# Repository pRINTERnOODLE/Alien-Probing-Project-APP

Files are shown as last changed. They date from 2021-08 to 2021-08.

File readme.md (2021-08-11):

### APP Alien Probing Project

Design prompts for this mod are: 
- To provide a bed probing solution for the Tiny-M which requires no modifications to the core parts and no loss of X Y or Z axis travel.

Additional design parameters include: 
- Keep the design envelope unchanged (fit inside panels etc)
- NOT affect overall design beyond adding probe functionality.
- Printed parts must not require supports

The M3x5mm hex screws used on the "captive" MUST be alloy steel and must be either flat head or cap head in order to be magnetically attracted when attaching.

Typically no brim is required for the printed parts...EXCEPT FOR THE SHUTTLE (see print settings below)

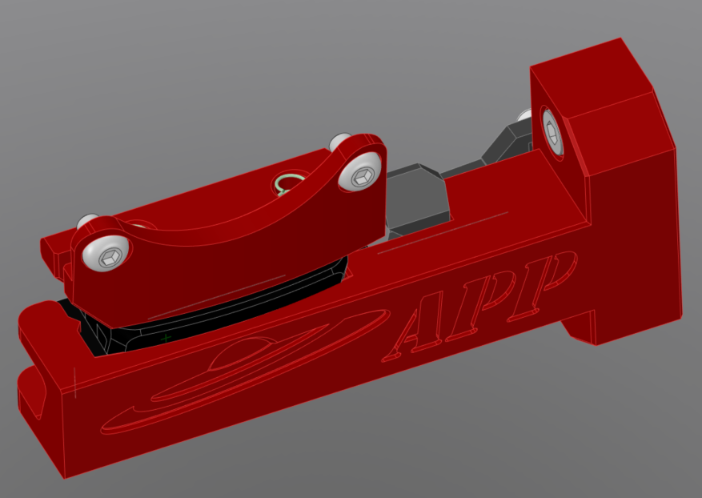
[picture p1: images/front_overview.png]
Front Overview


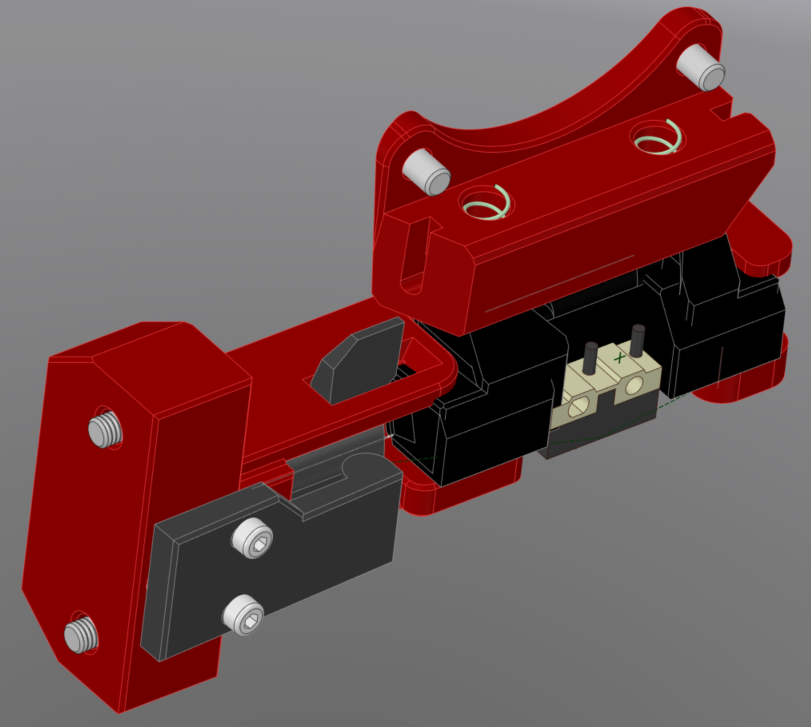
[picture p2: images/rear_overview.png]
Rear Overview


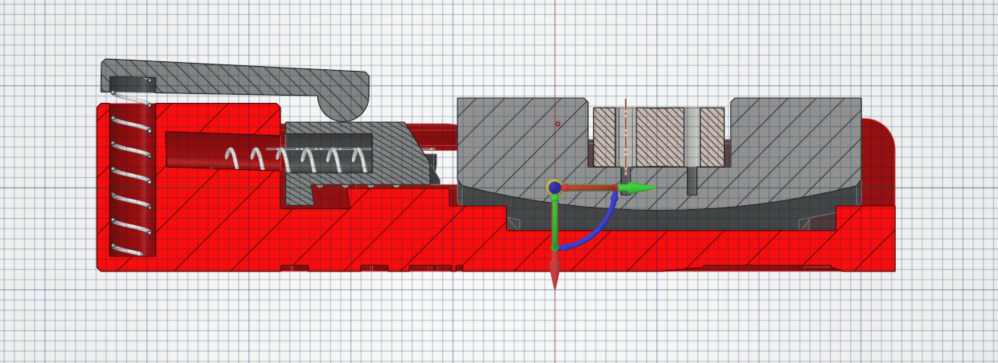
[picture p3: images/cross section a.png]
Cross Section A


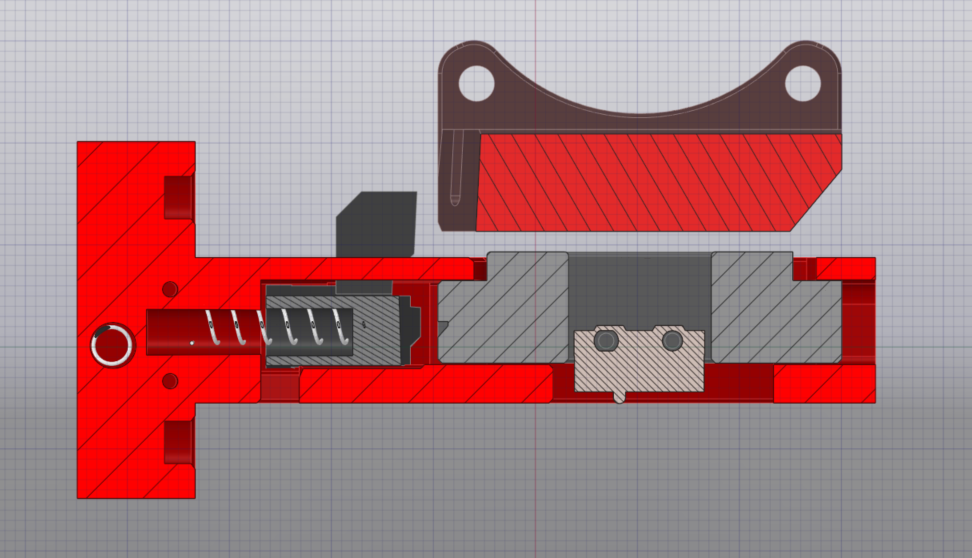
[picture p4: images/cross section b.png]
Cross Section B


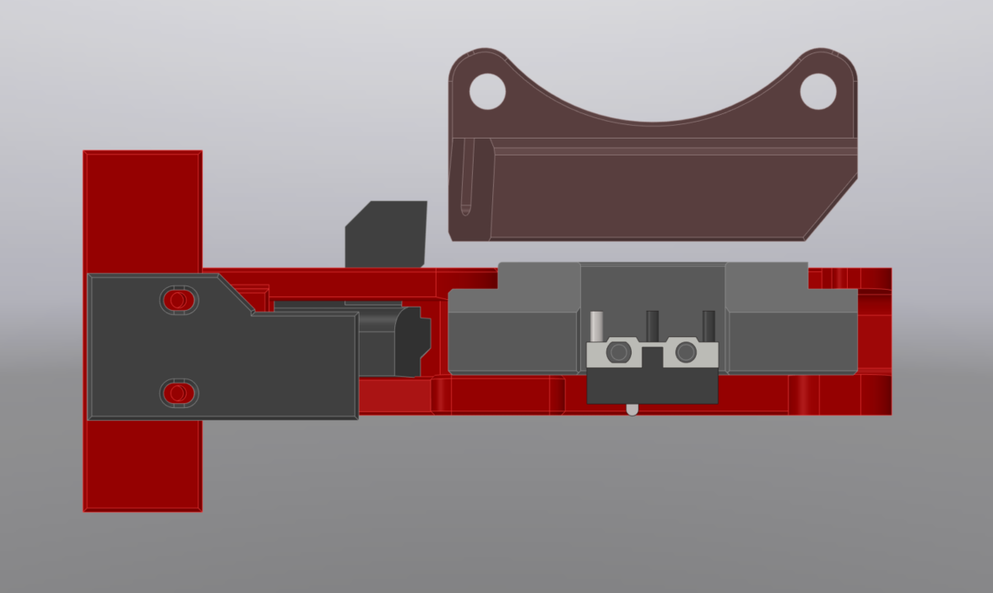
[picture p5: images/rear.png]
Rear


#### BOM (US Sources)

#### Hardware	
- 2x M3 Heat Set Nut		[Amazon](https://www.amazon.com/iplusmile-Embedment-Threaded-Printing-Projects/dp/B087NBYF65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)
- 2x M3 Roll In Tee Nut [Amazon](https://www.amazon.com/Boeray-Spring-Aluminum-Profile-20x20mm/dp/B075SY9Y96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)
- 2x M3x6 BHCS		[Amazon](https://www.amazon.com/Button-Socket-Drive-Screws-Stainless/dp/B07QDWFFX3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)

- 2x m3x14 SHCS     [Amazon](https://www.amazon.com/iExcell-Stainless-Socket-Screws-Wrench/dp/B089KQV2WV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)

- 4x m2x10 SHCS self tapping     [Amazon](https://www.amazon.com/Hexagon-Socket-Tapping-Screws-M2x10mm/dp/B00YBMROKC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)

- 3x m4x25 Pen spring   [Amazon](https://www.amazon.com/Customized-Galvanizing-Compression-Diameter4mm-Diameter25mm/dp/B08P8Z1J5S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)

- 2x m3x6 Neodimium pancake magnets [Amazon](https://www.amazon.com/Round-Multi-Use-Magnets-Refrigerator-Project/dp/B07G7ZMGT5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)

- 1x OMRON D2F-01F (or similar Microswitch SPDT Subminiature) [Amazon](https://www.amazon.com/D2F-01F-Switch-Microswitch-Subminiature-Logitech/dp/B0062WNDLI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)

### ABS Print Settings

#### If printing all at once:
- 0.2 layer height
- 5 walls 
- 5 top/bottom layers
- 40% infill (cubic)
- moderate print speed
- 0.3 Z-hop
- no supports
- 10 line brim only on shuttle

#### If printing just the shuttle:
- 0.2 layer height
- 3 walls 
- 2 top/bottom layers
- 100% infill (zigzag)
- SLOW print speed (10mm/s or less is good)
- no Z-hop
- no supports
- 10 line 
- modereate cooling

### Assembly & Physical Install Guide

- step one

Install the magnets in the "spaceship", strip some wire for connecting to the main control board, and cut ONE of the pen springs in half.

inatall magnets

- step two

Install your wires going from the main board to the tool head

install wires

- step three

Install the two cut springs into the spring holes on top of the wires and magnets (optionally solder the wires to the springs)

install springs

- step four

Install the 2x m3 heat set nuts on the bottom holes of the extruder fan and screw the "spaceship" assembly on the tool head and terminate your probe wires to your main board.

install het set nuts

install spaceship

- step five

Install the Micro switch onto the "captive" making sure the switch pin is in correct alignment with the nozzle (machine right)

install switch

- step six

Cut and strip two small wires which will go from the microswitch to the screw "terminals". Solder each of the wires to the switch terminals marked COM and NC. The terminal post side of the wires can be wrapped around the post screws clockwise, or the wire can go in the screw hole followed by the screw.

install wires

install more wires

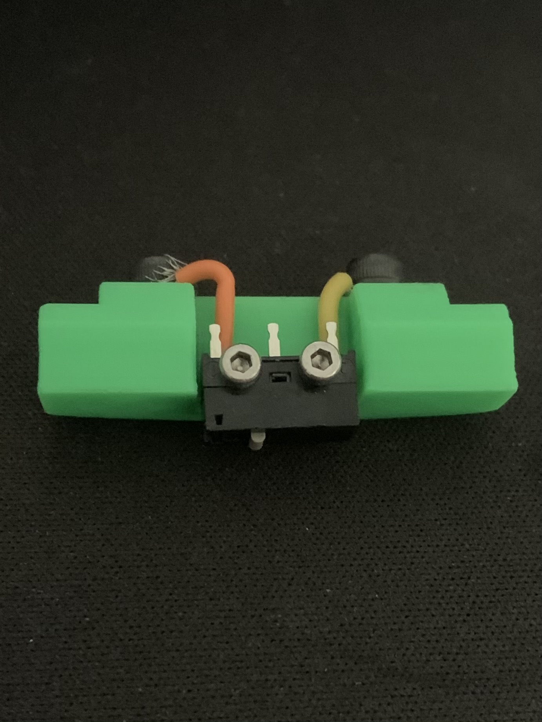
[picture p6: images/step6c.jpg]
install all the wires


- step seven

Install the two remaining m4x25 pen springs

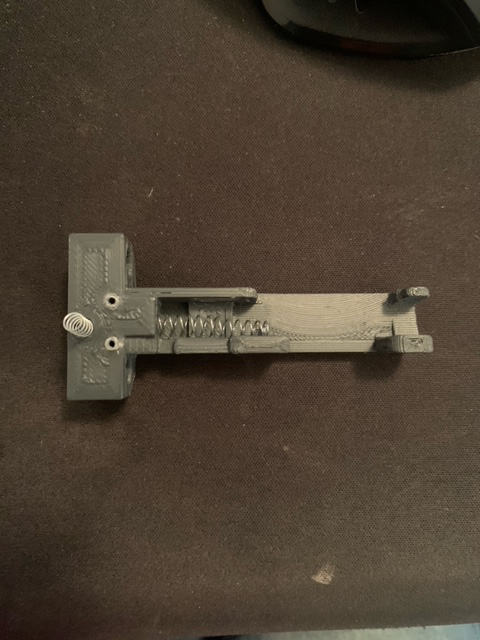
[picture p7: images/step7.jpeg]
install the main springs


- step eight

Install the shuttle onto the shuttle spring

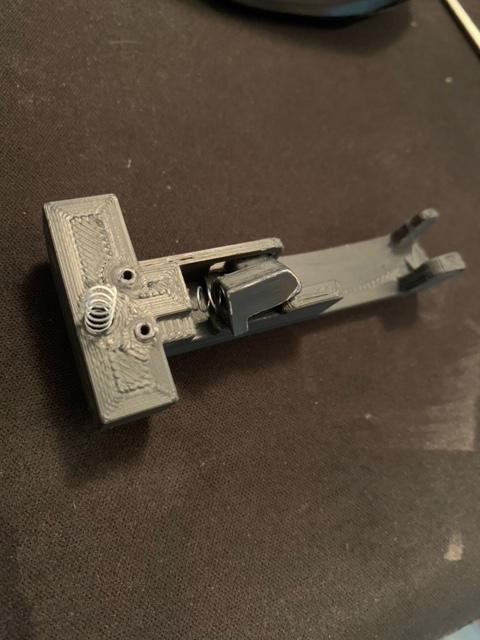
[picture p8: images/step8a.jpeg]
install the shuttle


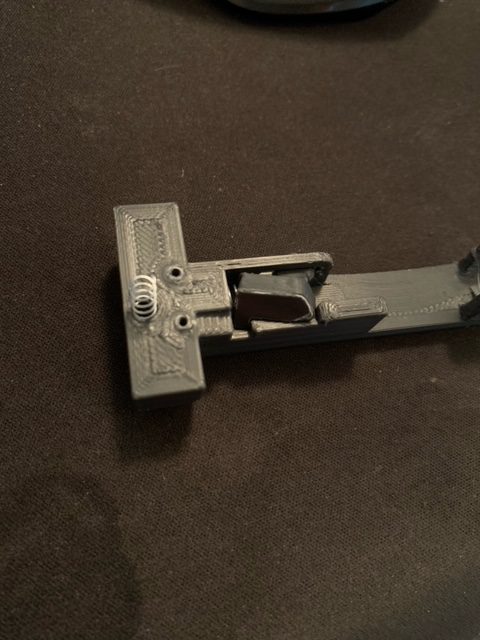
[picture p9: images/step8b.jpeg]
really install the shuttle


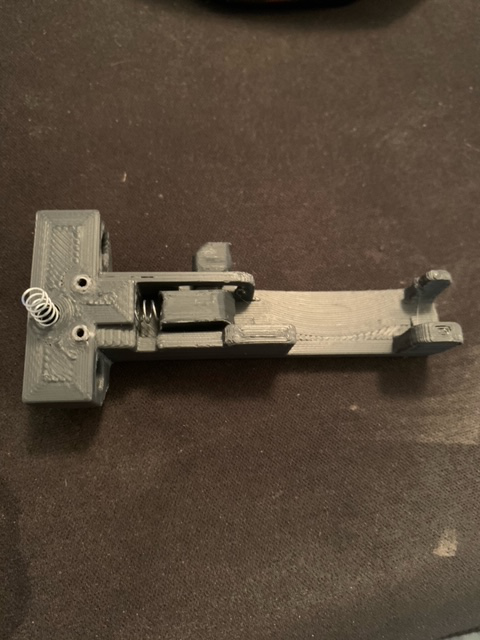
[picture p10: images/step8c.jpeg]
there you go...installed


- step nine

Thread both of the the self tapping screws all the way into the torsion spring arm and keep going untill they're stripped out and loose enough that they can wiggle a little.
Now back one of the screws almost all the way out and install the torsion spring arm onto the torsion spring one screw at a time.

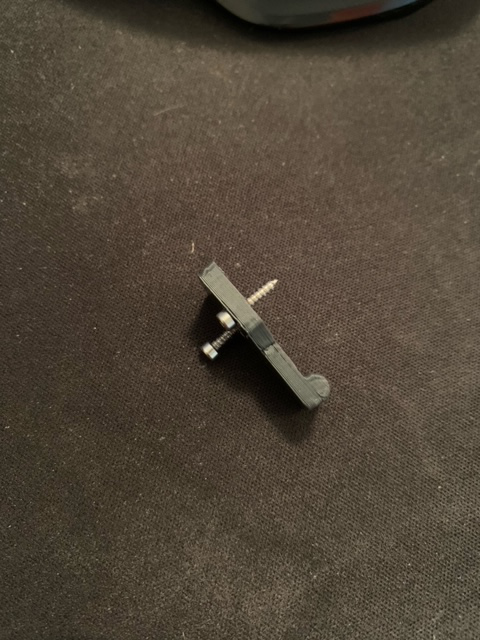
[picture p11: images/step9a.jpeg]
strip those screws


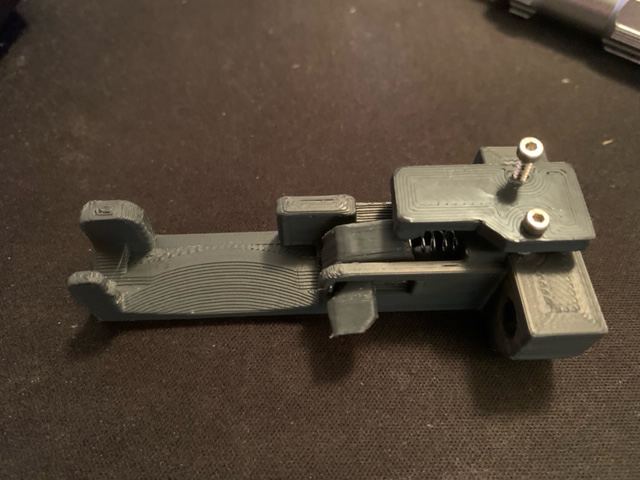
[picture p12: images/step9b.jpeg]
install install install


- step ten

Assemble the "captive" into the "home planet" and make sure the locking mechanism works to retain the captive. Now, WITH THE "CAPTIVE" LOCKED IN, adjust the torsion spring arm screws until there's very little room between the "torsion spring arm" and the "home planet"...do not bottom out this adjustment or binding and failure will result.
Lock and unlock the shuttle a few times and loosen off the torsion spring arm screws as needed for proper operation.

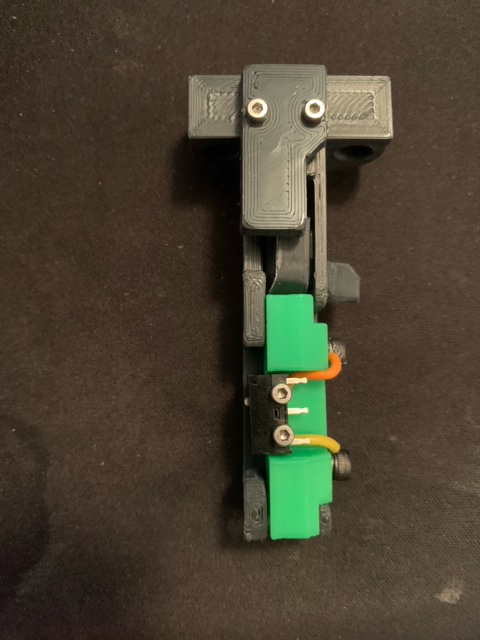
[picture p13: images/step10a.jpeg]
put it all on the machine


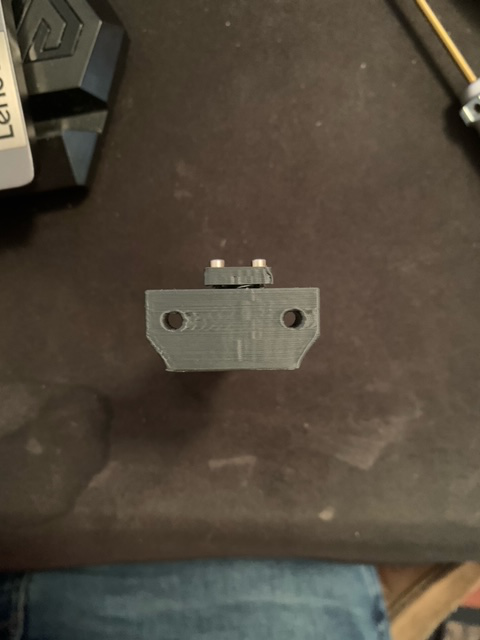
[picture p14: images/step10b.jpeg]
yes we're close now


- step eleven

With the "captive" installed and locked in place loosly attach the entire "home planet" assembly to the right front upright 2020 extrusion low enough that the tool head will miss it when moved forward.

With the power to the printer off, move the tool head forward and to the right so you can line up the "home planet" as you screw it on. The best alignment is when the "captive" screws just kiss the plastic of the "spaceship" as the tool head is moved forward...this alignment should "lift" the captive slightly and lock it in place on the tool head when properly set up. Leveling the "captive" screws can help this alignment (screw them in or out relative to eachother). 

With the power still off, unlock the captive by sliding the "shuttle" to the right and slowly move the tool head in and out of the docking possition checking for smoth operation. The "captive" should not get bumped off or hang up on the way in or out...adjust as needed.

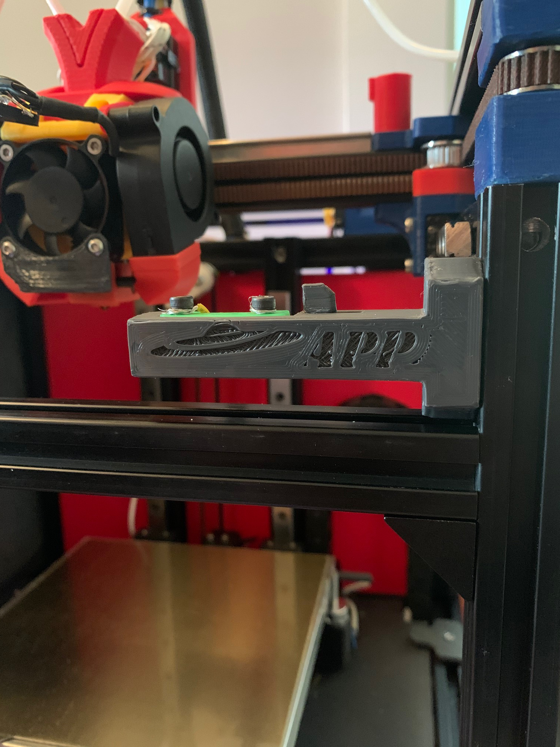
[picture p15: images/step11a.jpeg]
check alignment


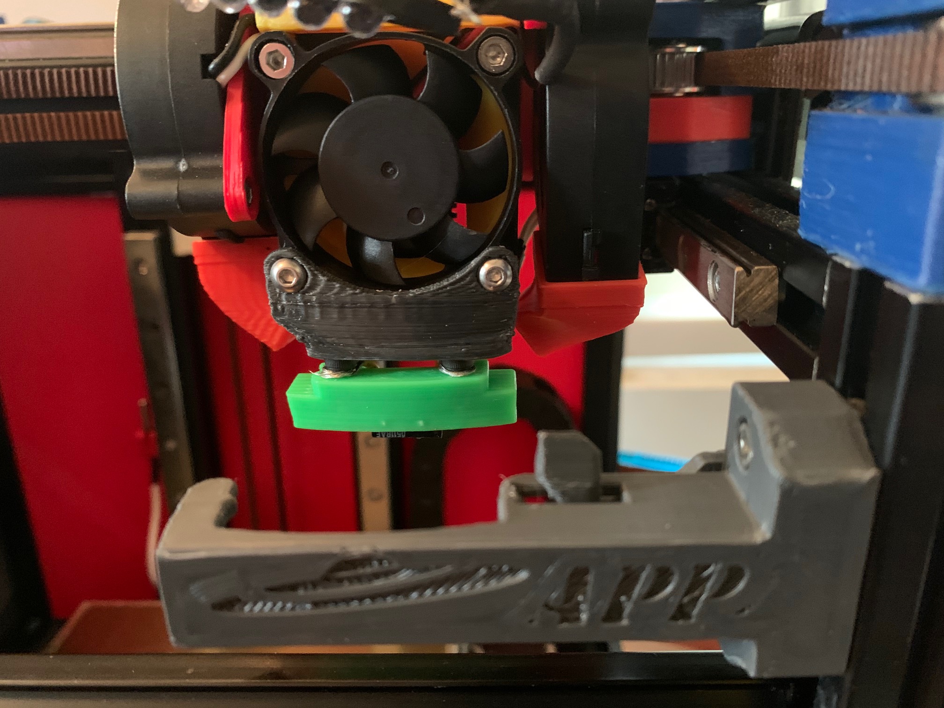
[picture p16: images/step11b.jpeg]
check agian


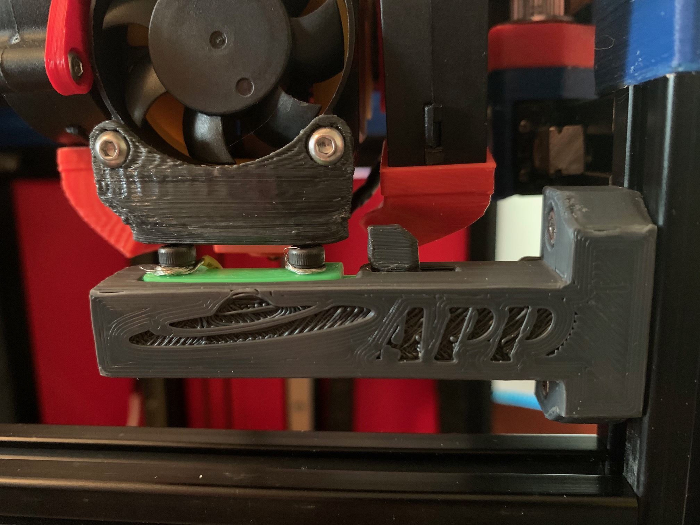
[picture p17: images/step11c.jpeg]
check and adjust till it looks good


### Firmware Setup

1. REMOVE THE "CAPTIVE" probe switch from the "home planet" and grab a pen and paper.

2. power on

3. home x y z

4. move bed down 20mm or more

5. manually command the tool head toward the front right corner (x130 y20 ish for a standard 150mm Tiny-M)

6. move the tool head write down the coordinate where the edge of the "spaceship" and the edge of the "shuttle" line up in X (mine is X150)

7. write down the coordinate where the edge of the "spaceship" and the edge of the "shuttle" line up in Y (mine is Y5)

8. now write down the same Y coordinate PLUS 12mm (mine is Y17 )

9. from the point in step 7, move the tool head ONE MM at a time in X+ (right) untill the shuttle is locked open. Write this absolute coordinate down (mine is X153 Y5).

10. move the tool head back about 4mm in X- (to the left) and place the "captive" probe switch into the "home planet" under the tool head...the probe should click in place under the tool head firmly onto the magnets (mine is X148.5 Y2). Write this coordinate down.

11. move the tool head and attached probe in -Y (forward) and write down where the probe makes contact with the "home planet" (mine is X148.5 Y1)

12. move the tool head and probe in Y+ (to the back) about 20mm (my coordinate for this is X149 Y25) observing the "captive" for smooth operation. Move it back and forth a few times. Adjust the tool head in X if needed untill you can move the probe in and out of the home planet along Y withot binding or shifting the "captive". Some fiddling with the "home planet" might be needed here to get it just right.

13. move the tool head and probe into the "home planet" (coordinate from step 10)

14. now move the tool head in -X (to the left) 10mm. This is the detachment coordinate (mine is X138.5 Y2). The probe should detach and remain home. If successful move on to step 15. If you hear a thump and or the probe flies out...move the "home planet" down very slightly until disengagement is smooth and recheck step 12. 

15. now that you can move to the detachment coordinate and smoothly detach the probe, move the tool head in Y+ (back) 10mm and write this coordinate down (mine is Y11).

16. move the tool head in X+ (to the right) to the X coordinate in step 9 (mine is X153)

17. lock the "captive" in place by moving the tool head 1mm at a time in -Y (forward) untill the shuttle clicks and locks the captive in place (mine is X153 Y7).

#### RRF Example
Now two custom macros can be written

;load.g

; called to load the APP

G90                     ;   absolute moves

G1 X150 Y17 F99999      ;   coordinate from step 6 and 8

G1 Y5 F2000             ;   coordinate from step 7

G1 X153                 ;   coordinate from step 9

G1 X148.5               ;   coordinate from step 10

G1 Y2                   ;   coordinate from step 11

G1 Y17                  ;   coordinate from step 8

;unload.g 

; called to unload the APP

G90                     ;   absolute moves

G1 X148.5 Y17 F99999    ;   coordinate from step 6 and 8

G1 Y1 F2000             ;   coordinate from step 11   

G1 X138.5               ;   coordinate from step 14

G1 Y11                  ;   coordinate from step 15

G1 X153                 ;   coordinate from step 16

G1 Y7                   ;   coordinate from step 17

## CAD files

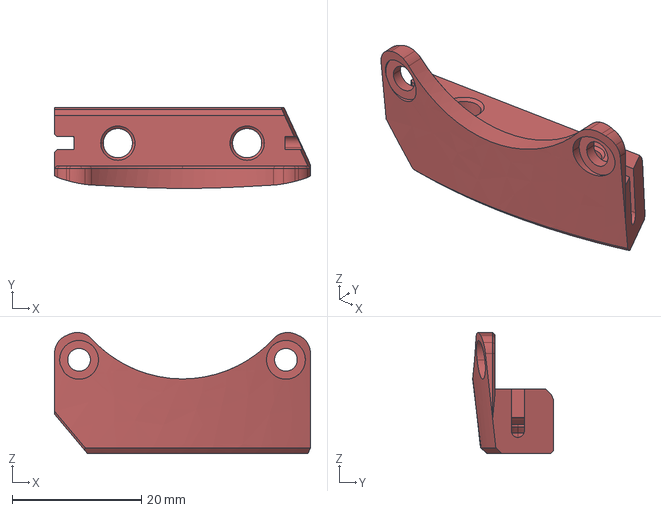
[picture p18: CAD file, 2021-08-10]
2.0 cad/STEP/spaceship.stp
39.6 x 12.5 x 18.7 mm

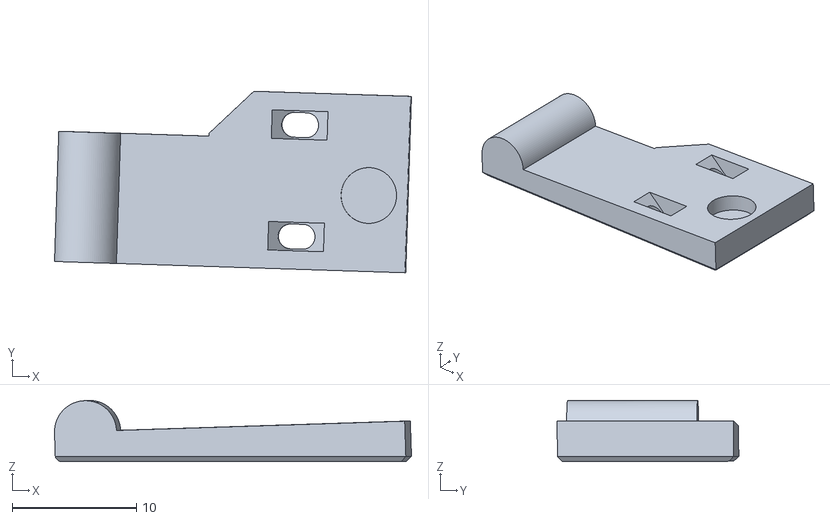
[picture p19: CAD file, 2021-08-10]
2.0 stl/torsion spring arm.stl
28.8 x 14.6 x 4.92

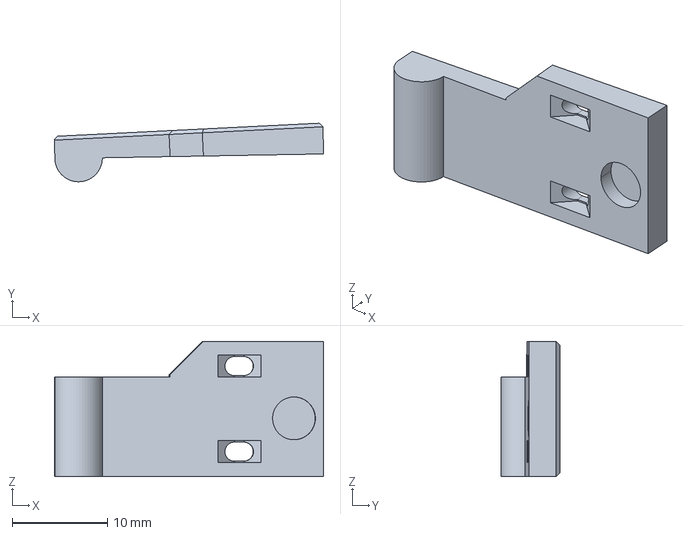
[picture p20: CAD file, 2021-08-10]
2.0 cad/STEP/shuttle trigger.stp
28.3 x 6.17 x 14.2 mm

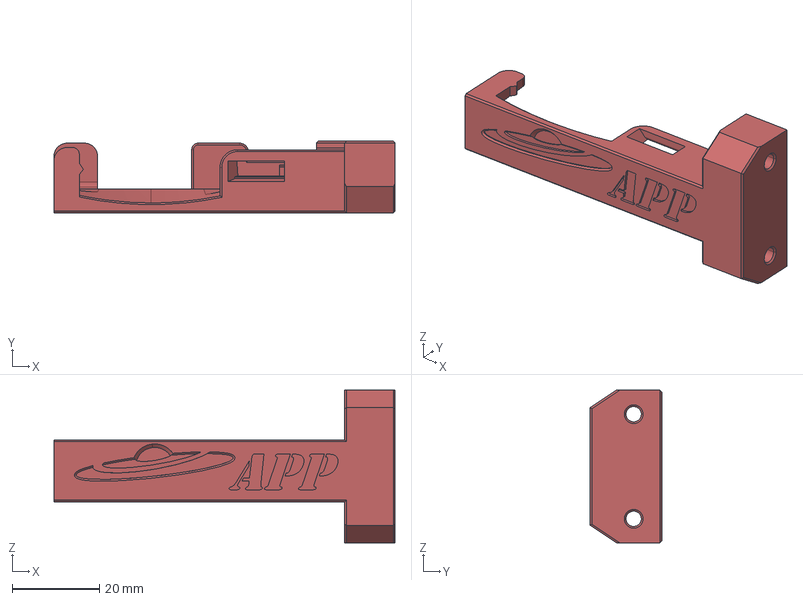
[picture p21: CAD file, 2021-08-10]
2.0 cad/STEP/home_planet.stp
78.3 x 16.5 x 35.0 mm

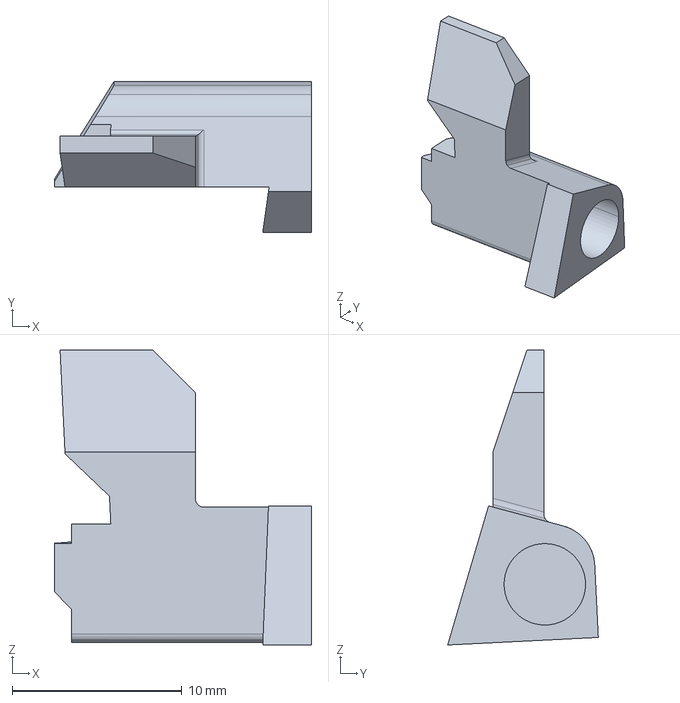
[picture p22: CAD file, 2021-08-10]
2.0 cad/STEP/shuttle.stp
15.2 x 8.88 x 17.4 mm

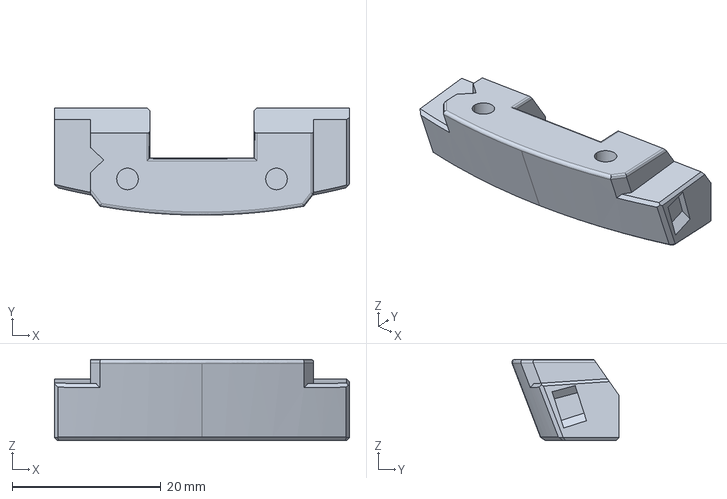
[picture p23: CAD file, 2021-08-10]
2.0 cad/STEP/captive.stp
39.6 x 14.4 x 10.9 mm

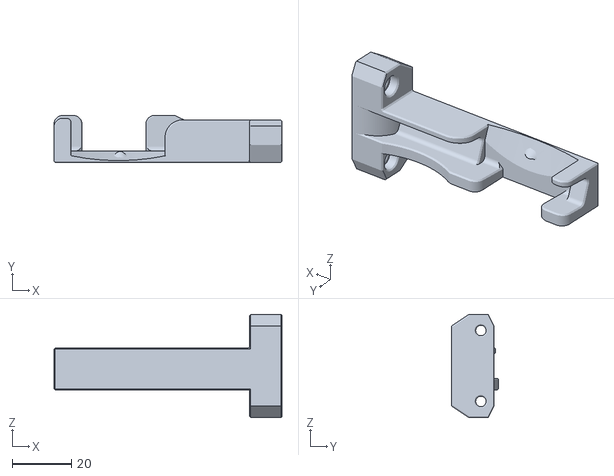
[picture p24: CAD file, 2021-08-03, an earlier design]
old.stl/home_planet_nologo.stl
77.2 x 16.0 x 35.0

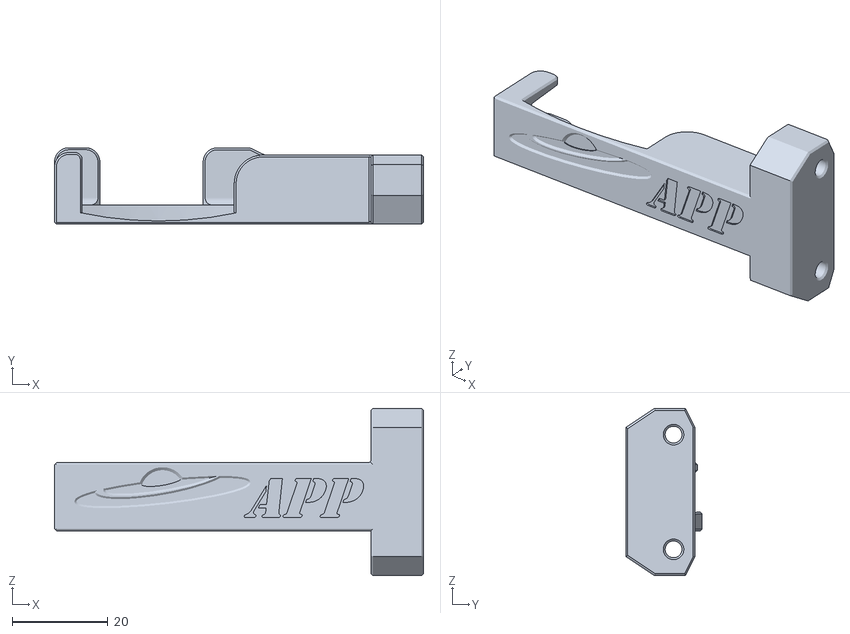
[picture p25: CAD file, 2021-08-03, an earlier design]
old.stl/home_planet.stl
77.2 x 16.0 x 35.0

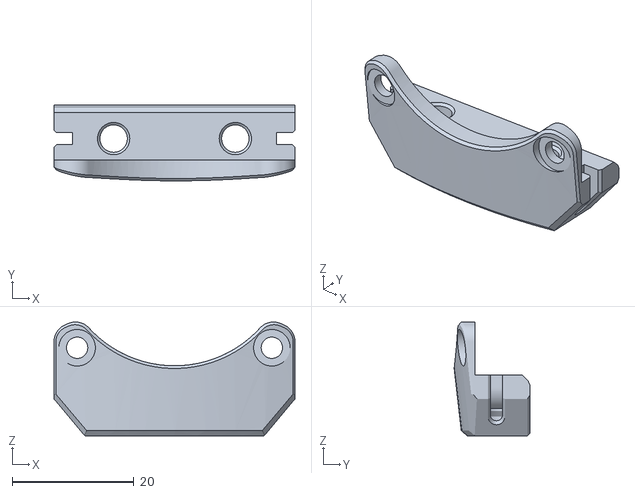
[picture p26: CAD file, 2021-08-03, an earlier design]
old.stl/spaceship.stl
39.6 x 12.5 x 18.7

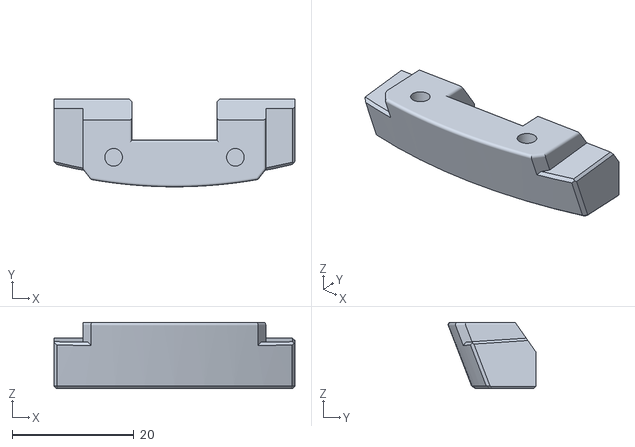
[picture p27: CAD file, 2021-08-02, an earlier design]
old.stl/screw style captive.stl
39.6 x 14.4 x 10.9

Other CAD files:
2.0 stl/captive.stl
2.0 stl/home planet.stl
2.0 stl/shuttle.stl
2.0 stl/spaceship.stl

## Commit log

2021-08-01 Beta Version of all files upload
    [captive.stl, home_planet.stl, spaceship.stl]
2021-08-01 Create STL dir
    [captive.stl, home_planet.stl, spaceship.stl]
2021-08-01 Update to clear stock fan duct
    [captive.stl]
2021-08-02 Update captive.stl
    More clearance
    [captive.stl]
2021-08-02 Update captive.stl
    fillet update
    [captive.stl]
2021-08-02 Create screw style captive.stl
    No bottom magnets required....positive wire attachment
    [screw style captive.stl]
2021-08-02 Update screw style captive.stl
    added stand off supports
    [screw style captive.stl]
2021-08-02 Update screw style captive.stl
    screw depth reduction
    [screw style captive.stl]
2021-08-02 Update screw style captive.stl
    Change screw size
    use 3mm carbon steel
    [screw style captive.stl]
2021-08-02 abandon quad magnet design in favor of screws
    screws .... not magnets
    [home_planet.stl, screw style captive.stl, spaceship.stl]
2021-08-03 update for fitment of screws
    Screw head fitment on spaceship
    [spaceship.stl]
2021-08-03 Logo no logo
    One has it one does not
    [home_planet.stl, home_planet_nologo.stl]
2021-08-03 file names
    [home_planet.stl, home_planet_nologo.stl]
2021-08-09 upload V2.0
    Now with anti abduction locking mechanism!!
    [captive.stl, home planet.stl, shuttle.stl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]
2021-08-09 images from gad
    images showing assembly and cross sections
2021-08-09 correct orientation for printing
    [shuttle.stl]
2021-08-09 fitment for docking
    [home planet.stl]
2021-08-09 printing orientation
    [torsion spring arm.stl]
2021-08-10 step files & updated stls
    more minor refinements and step files
    [captive.stl, captive.stp, home planet.stl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]
2021-08-10 Some assembly images
